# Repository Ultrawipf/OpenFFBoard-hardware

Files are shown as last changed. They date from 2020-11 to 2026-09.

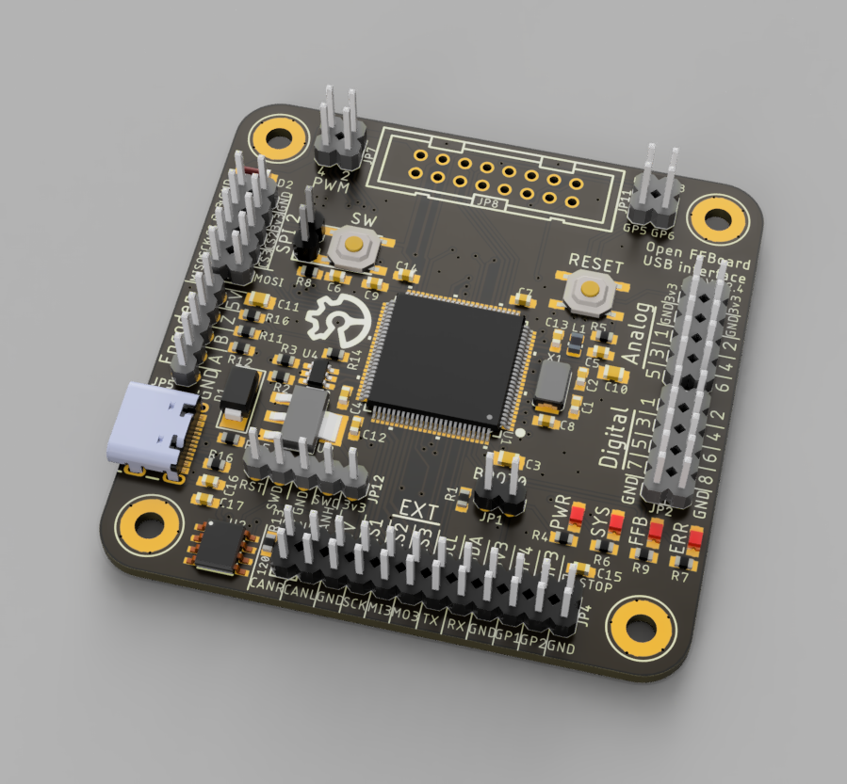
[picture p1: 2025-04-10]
OpenFFBoard-main/V1.2.4 F407/3D/OpenFFBoard_F407_1.2.4_render1.PNG

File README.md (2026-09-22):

# OpenFFBoard-hardware
This contains the hardware designs of the OpenFFBoard

These are work in progress.
No guarantee for functionality or safety! The designs are experimental and may change at any time.
The firmware is available in the main [OpenFFBoard](https://github.com/Ultrawipf/OpenFFBoard) git.

This project requires soldering of many fine pitched parts including QFN. Availability of components may change over time so check for alternatives if something is not available.
The motor driver should be made with 2oz copper layers for best thermal performance!

The firmware may run on some third party development kits but as they have different pinouts and missing peripherals this is not recommended.

## Buy official kits
* [Elecrow](https://www.elecrow.com/open-ffboard-stm32f407-usb-interface-only.html)
* [Lectronz](https://www.lectronz.com/stores/gigawipf)
* [Tindie](https://www.tindie.com/stores/gigawipf/) or Discord.

Check the [Discord](https://discord.com/invite/gHtnEcP) and [project page](https://hackaday.io/project/163904-open-ffboard) for updates.

---

### LICENSE NOTE: The root license applies to all subfolders NOT containing their own LICENSE file. If a subfolder contains a different LICENSE file this different license applies to all subfolders below this LICENSE file.

**If you want to sell any hardware of this project yourself i would kindly ask you to get in contact with me ([mail](mailto:ffboard@y-richter.de) or Discord)**

## Changelog
### TMC Driver:

#### 1.1: (Prerelease prototype)
- Added filtering for Hall and Encoder inputs.
- Separated TMC and STM VM sense dividers

#### 1.2: (Major redesign)
- Using TMC4671-LA production version
- Added 5V buck converter
- Added emergency shutdown method by pulling enable low
- Rotated power stage. Moved all motor connectors to one side
- Moved analog encoder pins and routed differential inputs out
- Improved vcore impedance
- Increased encoder filter frequencies
- Reduced resistance of sense dividers
- Switched LM5050 to LM74700
- Space for 2 VM capacitors
- Improved mosfet protection
- Added temperature sensor pads on AGPI-B
- 50x50+100mm screw holes

#### 1.2 fix:
- Fixed silkscreen (R18 and R19 swapped)
- Modified some labels
- Added 33k gate pulldown for brake resistor
- Moved and resized vias in motor driver part (Manufacturing reliability)
- Tented vias

#### 1.2.2 (HALL):
- Redesigned power stage to use hall sensors (LEM GO SME and TMCS1100)
- Changed buffers to 74LV17APWJ
- Added opamp for TMC inputs (temperature and voltage sensing)
- Used opamp as comparator for hardware brake resistor activation point (~65V)
  
### 1.3.3:
- Analog section with separate LDO
- Support for more current sensors (ACS724)
- Optimized gate driver circuit w. resistors and diodes
- More separation between analog and power sections

### STM USB Interface:
#### 1.1:
- Initial prototype
- STM32F411RE based
- Only supports TMC4671 driver
- Only one SPI2 CS

#### 1.2:
- STM32F407VG
- Reserved PWM pins
- 3 CS pins per SPI
- CAN bus
- Reserved E-Stop
- USB Vbus sense
- separated ADCs for vsense and analog in
- LEDs moved
- Added FFBoard logo
- Changed USB diode to SMC
- Added zener pad on 5V
- Removed encoder buffer
- Higher value pwr led resistor

#### 1.2.1:
- Fixed some labels
- Moved USB socket and terminals slightly to the corners (Big usb plugs might interfere with the pins)
- Changed crystal load capacitors to lower values. (F407 DFU is very sensitive and does not work reliably with too high value caps)
- Added E-Stop capacitor against noise triggering it
- Tented vias

#### 1.2.2
- Swapped (Previously unused) Encoder Z pin from pin 65 to pin 62 because of interrupt conflicts with the DRV flag pin

#### 1.2.3
- USB-C instead of micro USB
- SPI1 uses a 2 row header
- Additional USB protections

#### 1.2.4
- Moved EXT header slightly
- Used 2 extra jumper pins for CAN termination instead of solderjumper

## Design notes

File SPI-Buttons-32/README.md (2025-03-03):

# Shift register button module

This module allows the connection of up to 32 (or more if chained) buttons to any spi capable microcontroller or as a button source in the OpenFFBoard firmware.

### Connections
* V+ - 3,3V (or 5V)
* OUT - MISO of controller
* CS (Latch) - CS pin of controller
* CLK - SCK
* GND - GND

* IN - OUT of previous module
* Buttons between GND and any input pin

### Configuration in OpenFFBoard

Select SPI button source, select 74HC165 mode and invert buttons and the amount of used buttons (up to 32 for 1, up to 64 for 2 modules)

### CS options

In the default configuration MISO is active with CS HIGH (Bare 74HC165 compatible mode).
Connecting R34 instead of R33 changes this to CS LOW active (SPI compatible mode).
The tristate output mode can be disabled by removing R35.

Mode | R33 | R34 | R35
-|-|-|-
CS HIGH w. tristate | ✅ | ❌ | ✅
CS LOW w. tristate | ❌ | ✅ | ✅
CS HIGH wo. tristate | ✅ | ❌ | ❌
CS HIGH wo. tristate | ❌ | ✅ | ❌

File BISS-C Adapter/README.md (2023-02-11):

## BISS-C module

This module allows the OpenFFBoard to use its SPI3 (EXT) header to communicate with common BISS-C encoders like the JKD-4-22PF-G05BL (used on Mige motors).

The SUB-D 15 female connector matches the pinout of Mige motors and some others directly.

The CS pin connection is optional. When left disconnected or low the transceivers are active, when high the transceivers are off.

The BISS-C encoder module can only be used with certain motor driver modes:

-   TMC via forwarding

-   VESC as secondary encoder

-   PWM

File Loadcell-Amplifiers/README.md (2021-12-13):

## INA333 3-wire Loadcell amplifier

Connections:
###
- Vin   :   3.3V/5V supply and load cell positive
- GND   :   GND and load cell negative
- IN    :   Load cell center/signal
- OUT   :   Amplified signal. Connect to ADC input

Gain setting: 10-1000, Clockwise rotation to increase
Offset: Clockwise to move the output up, ccw to move the output down to GND

Retune the offset when changing the gain and carefully check the output voltage to get the offset perfect.

The CPL and BOM files contain LCSC part numbers and be used on [JLCPCB](jlcpcb.com/).

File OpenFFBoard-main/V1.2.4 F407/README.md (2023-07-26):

### FFBoard main USB interface F407VG
This is the heart of the Open FFBoard.
It runs the FFBoard firmware and interfaces with all your peripherals and motor drivers.

V1.2.3 and 1.2.4 is a USB-C version and adds additional USB protections.
The SPI1 port layout had to change to 2 rows instead of 1.

#### How to order yourself
You can order this board directly via [jlcpcb.com](https://jlcpcb.com/?from=Gigawipf).

The BOM and component placement files are available in the JLC assembly folder and already formatted with matching LCSC part numbers.

Everything apart from the headers can be directly assembled by JLC including the USB socket.

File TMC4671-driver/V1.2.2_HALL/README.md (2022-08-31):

# OpenFFBoard TMC4671 driver 1.2.2

Note: this is an experimental version for testing hall sensors. The 1.2 is shunt based.

Some parts may be difficult to source. The manufacturing files were made during a time where alternatives had to be found for some parts.

For the TMC1100 the SJ1 and SJ2 2.5V ref jumpers must be shorted. The LEM GO provides its own reference and the SJ1 and SJ2 must be left disconnected for best noise performance and C27 and C28 MUST be left blank!

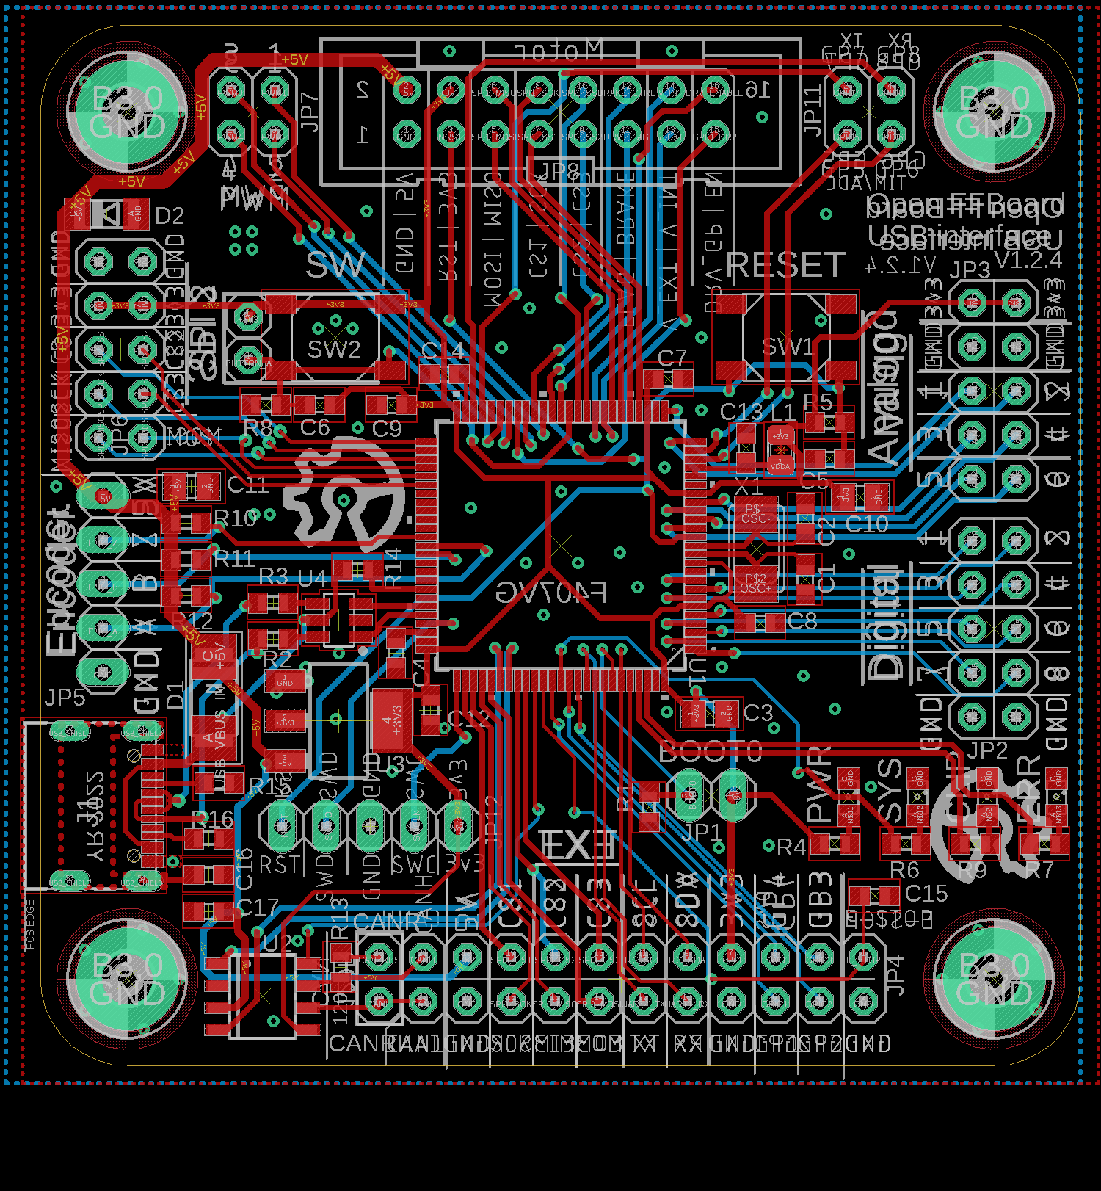
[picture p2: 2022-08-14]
OpenFFBoard-main/V1.2.4 F407/board.png

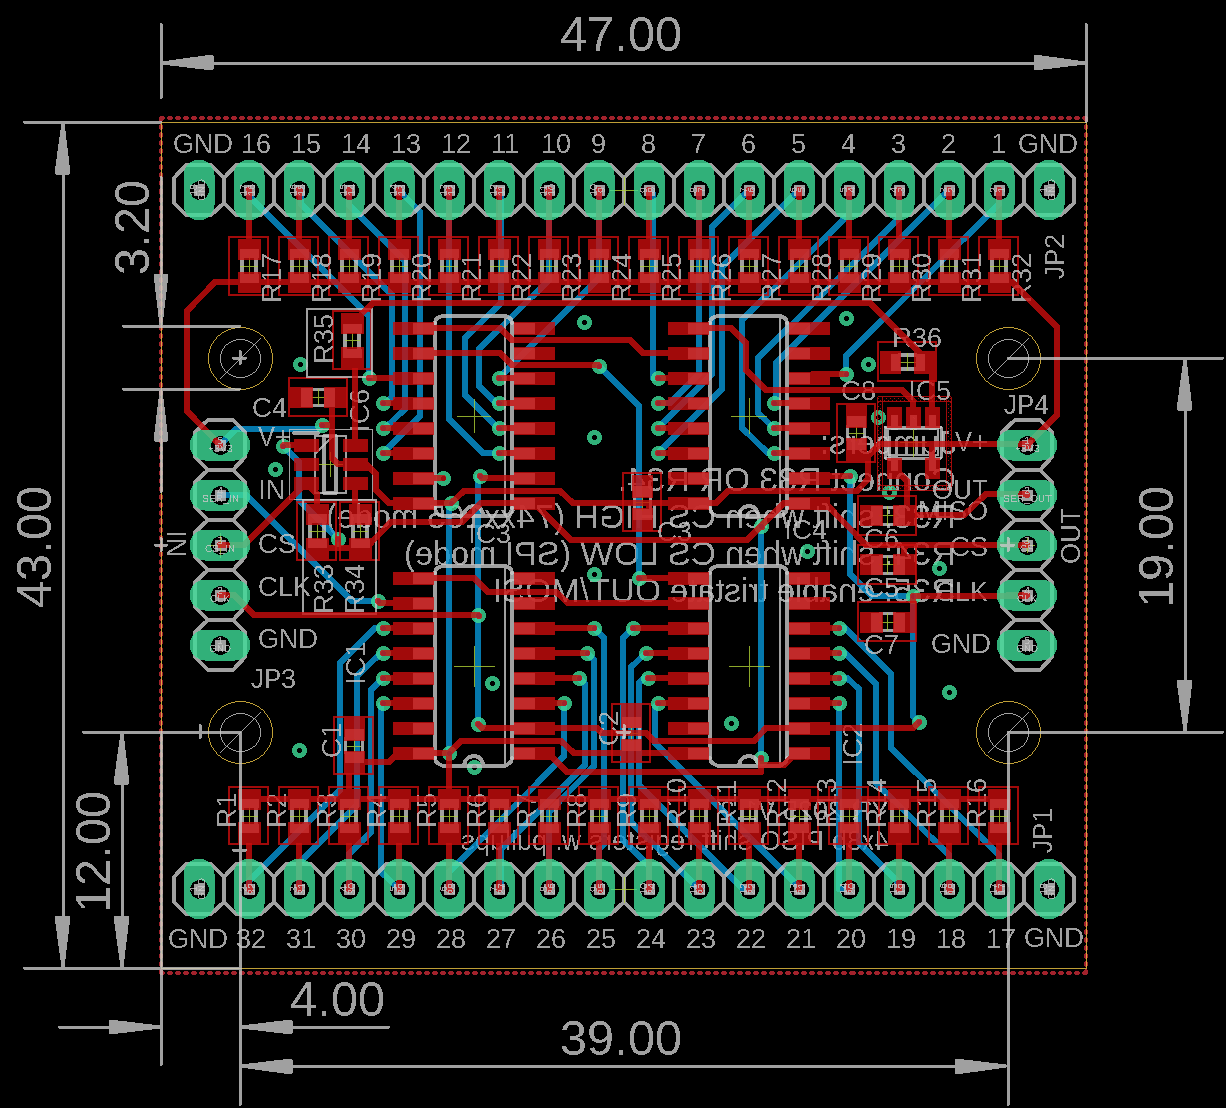
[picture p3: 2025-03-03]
SPI-Buttons-32/pcb.png

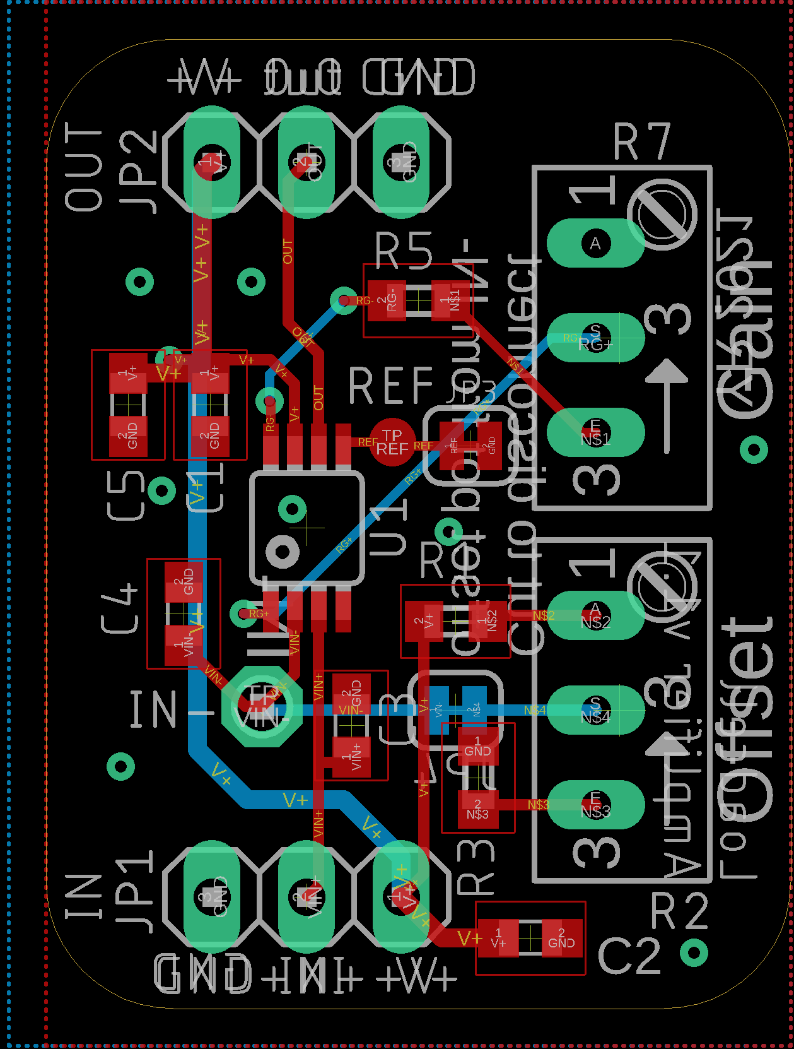
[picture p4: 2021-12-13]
Loadcell-Amplifiers/boardview.png

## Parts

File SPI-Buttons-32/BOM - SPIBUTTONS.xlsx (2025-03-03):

Comment | Designator | Footprint | LCSC Part #
1x18 pinheader | JP1, JP2 | 1X18
1x5 pinheader | JP3, JP4 | 1X05
10k resistor | R1, R2, R3, R4, R5, R6, R7, R8, R9, R10, R11, R12, R13, R14, R15, R16, R17, R18, R19, R20, R21, R22, R23, R24, R25, R26, R27, R28, R29, R30, R31, R32,R36 | R0603 | C25804
1µF capacitor | C1, C2, C3, C4,C8 | C0603 | C15849
74HC165D | IC1, IC2, IC3, IC4 | SO16 | C5613
0R | R35,R33 | R0603 | C21189
SN74LVC2G14DBV | IC6 | SOT23-6 | C12401
74LVC1G125DBV | IC5 | SOT23-5 | C23654

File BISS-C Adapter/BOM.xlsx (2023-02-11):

Comment | Designator | Footprint
SUB-D | X1
5p header 90° | JP1
100nF | C1, C2 | C0603
4.7uF | C3 | C0603
RS485 transceiver | IC1, IC2 | SOIC-8
10k | R1,R2 | R0603
Nmos | Q1 | SOT-23

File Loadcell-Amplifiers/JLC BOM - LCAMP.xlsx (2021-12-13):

Comment | Designator | Footprint | LCSC Part #
INA333 | U1 | MSOP-8 | C19450
10k pot | R2,R7 | THT | C118954
1µ Capacitor | C2,C3,C5 | C0603 | C15849
4.7k Resistor | R1, R3 | R0603 | C23162
47 Ohm Resistor | R5 | R0603 | C23182
100n Capacitor | C4, C1 | C0603 | C14663

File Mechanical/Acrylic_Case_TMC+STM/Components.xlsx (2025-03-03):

Amount | Type | File/Link
1 | Bottom cover 3mm clear acrylic | Bottom_nosides.dxf
1 | Top cover 3mm clear acrylic | Top_nosides.dxf
6 | Nylon M3x6 screw
6 | Nylon M3 nut
10 | Nylon M3x6+6 Standoff
2 | Nylon M3x18+6 Standoff
2 | 0.5mm or 0.6mm M3 washer

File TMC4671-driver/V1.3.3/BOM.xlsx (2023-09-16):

Comment | Designator | Footprint | Notes
3.3V Ldo 1117 | U21 | SOT223
1.5k | R16, R22, R24, R29, R31, R40, R41, R42 | R0603
100nF | C1, C3, C4, C5, C6, C7, C8, C15, C16, C17, C19, C20, C21, C22, C23, C24, C26, C33, C35, C36 | C0603
10k | R2, R3, R15, R17, R18, R26, R28, R46 | R0603
ERTJ1VR103J | R30 | R0603 | digikey https://www.digikey.de/en/products/detail/panasonic-electronic-components/ERT-J1VR103J/269353 lcsc C525381
10µH LQH43PN100M26L | L2 | L4532P | digikey
4.7nF | C42, C43,C29, C30, C31 | C0603 |  | Depends on sensor variant
1µF | C11, C12, C13, C14, C37 | C1206
15 | R4, R5, R6, R7, R8, R9, R10, R11 | R0603
220µH 74404084221 | L1 | 8MM INDUCTOR | digikey
25MHz | Y1 | ECS-327KE-TR
294k | R25, R27, R43 | R0805
33k | R12, R13, R14, R20, R21 | R0603
4.7k | R34, R35, R36, R37, R38, R39 | R0603
10µF | C2, C18, C25, C32, C34, C39, C41 | C0805
47k | R33 | R0603 |  | Brake resistor emergency point
593D476X0016D2TE3 | C38 | CAPPM7343X310N
680µF EEU-FS1K681B | C9, C10 | E7,5-16 | https://www.digikey.de/en/products/detail/panasonic-electronic-components/EEU-FS1K681B/9597098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 | https://www.arrow.com/en/products/eeu-fs1k681b/panasonic?q=EEU-FS1K681B
71.5k | R23, R32, R44, R45 | R0805
74LV17APWJ | U19 | TSSOP14 | digikey
AP3012KTR-G1 | U24 | SOT23-5L
NTMFSC2D9N08H | U8, U9, U10, U11, U12, U13, U15, U16, U17,U22 | POWERTFDN8 | Or FDMS86181, BSC030N08NS5 (20ohm gates minimum)
BZX384-XXX | D6, D7, D8, D11 | SOD323-R
Green | LED1 | SML0805
HV >100V | D2, D3, D4, D5, D12, D14 | SOD-123FL | Must handle 500mA+
LM5109BSD | U2, U3, U4, U5 | SDC08A
LM74700-Q1 | U20 | SOT23-6 | https://www.digikey.de/en/products/detail/texas-instruments/LM74700QDBVTQ1/9953058
LV low drop diode (<10V) | D1, D9, D10, D16 | SOD-123FL | Fast gate discharge
max5035dasa | U23 | 8-SOIC
MCP1402T-E | U14 | SOT23-5L
MCP6004 | U18 | TSSOP14
TMC4671 | U1 | QFN76_10P5X6P5
5V LDO 1117 | U25 | SOT223
STPS30120DJF-TR | (U22) | PowerFLAT-5x6 | If no LM74700 is used. Otherwise use another mosfet here
SMA HV diode | D15 | SMA Diode | For DC converter
ACS724 (https://www.lcsc.com/product-detail/Current-Sensors_Allegro-MicroSystems-LLC-ACS724LLCTR-30AB-T_C141715.html) | U6,U7
0 | R50,R51,R47, R48 | R0603 | For ACS724
0 | sj1,sj2,SJ3 | R0805 | For ACS724
47k | R1 | R0603 | 5v FB for max5035D
15k | R49 | R0603

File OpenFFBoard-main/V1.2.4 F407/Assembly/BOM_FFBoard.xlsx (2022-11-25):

Comment | Designator | Footprint | LCSC Part #（optional）
3V3 LDO xx1117 | U3 | SOT223 | C6186 (https://lcsc.com/product-detail/Low-Dropout-Regulators-LDO_AMS_AMS1117-3-3_AMS1117-3-3_C6186.html/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)
100nF | C5, C6, C7, C8, C9, C12, C13, C15, C16, C17 | C0603 | C14663 (https://lcsc.com/product-detail/Multilayer-Ceramic-Capacitors-MLCC-SMD-SMT_YAGEO-CC0603KRX7R9BB104_C14663.html)
USB-C connector | J1 | USB-C | C319148
10k | R1, R5, R8, R14 | R0603 | C25804 (https://lcsc.com/product-detail/Chip-Resistor-Surface-Mount_Uniroyal-Elec-0603WAF1002T5E_C25804.html/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)
120 | R13 | R0603 | C22787 (https://lcsc.com/product-detail/Chip-Resistor-Surface-Mount_Uniroyal-Elec-0603WAF1200T5E_C22787.html/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)
1k | R4 | R0603 | C21190 (https://lcsc.com/product-detail/Chip-Resistor-Surface-Mount_Uniroyal-Elec-0603WAF1001T5E_C21190.html/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)
2.2µF | C4, C14 | C0603 | C23630 (https://lcsc.com/product-detail/Multilayer-Ceramic-Capacitors-MLCC-SMD-SMT_SAMSUNG_CL10A225KO8NNNC_2-2uF-225-10-16V_C23630.html/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)
22 | R2, R3 | R0603 | C23345 (https://lcsc.com/product-detail/Chip-Resistor-Surface-Mount_Uniroyal-Elec-0603WAF220JT5E_C23345.html/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)
15pF | C1, C2 | C0603 | C1644 (https://lcsc.com/product-detail/Multilayer-Ceramic-Capacitors-MLCC-SMD-SMT_Samsung-Electro-Mechanics-CL10C150JB8NNNC_C1644.html)
330 | R6, R7, R9 | R0603 | C23138 (https://lcsc.com/product-detail/Chip-Resistor-Surface-Mount_Uniroyal-Elec-0603WAF3300T5E_C23138.html/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)
5.1k | R10, R11, R12, R15, R16 | R0603 | C23186
4.7uF | C3, C10, C11 | C0805 | C1779 (https://lcsc.com/product-detail/Multilayer-Ceramic-Capacitors-MLCC-SMD-SMT_SAMSUNG_CL21A475KAQNNNE_4-7uF-475-10-25V_C1779.html/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)
8MHz Crystal | X1 | NX5032 | C115962 (https://lcsc.com/product-detail/SMD-Crystal-Resonators_Yangxing-Tech-X50328MSB2GI_C115962.html/?href=jlc-SMT)
Ferrite | L1 | BLM21PG331SN1D | C1017 (https://lcsc.com/product-detail/Beads_Sunlord-GZ2012D601TF_C1017.html/?href=jlc-SMT)
LV Diode | D1 | SMADIODE | C2480 (https://lcsc.com/product-detail/Schottky-Barrier-Diodes-SBD_MDD-Microdiode-Electronics-SS14_C2480.html/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)
STM32F407VGT6 | U1 | LQFP100-14X14MM | C12345 (https://lcsc.com/product-detail/ST-Microelectronics_STMicroelectronics-STM32F407VGT6_C12345.html)
TJA1051T/3 | U2 | SOT96-1 | C38695 (https://lcsc.com/product-detail/CAN_NXP_TJA1051T-3-1J_TJA1051T-3-1J_C38695.html/?href=jlc-SMT)
Pushbutton | SW1, SW2 | 5.1mm | C318884 (https://lcsc.com/product-detail/Tactile-Switches_XKB-Connectivity-TS-1187A-B-A-B_C318884.html)
ZMM5V6 | D2 | MINIMELF | C8062 (https://lcsc.com/product-detail/Zener-Diodes_ST-Semtech-ZMM5V6_C8062.html)
blue | LED2 | CHIPLED_0805 | C189307
green | LED1 | CHIPLED_0805 | C2297 (https://lcsc.com/product-detail/Light-Emitting-Diodes-LED_Hubei-KENTO-Elec-C2297_C2297.html)
red | LED3 | CHIPLED_0805 | C84256 (https://lcsc.com/product-detail/Light-Emitting-Diodes-LED_Red-LED-SMDLED-80-180mcd_C84256.html/?href=jlc-SMT)
yellow | LED4 | CHIPLED_0805 | C2296 (https://lcsc.com/product-detail/Light-Emitting-Diodes-LED_Yellow-light-0805-Highlighted_C2296.html/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)
USB ESD protection | U4 | SOT-23-6 | C2827654

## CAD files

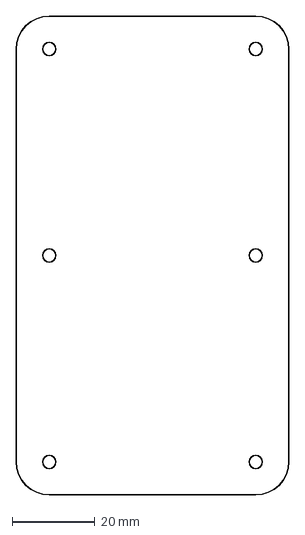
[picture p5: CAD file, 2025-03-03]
Mechanical/Acrylic_Case_TMC+STM/Bottom_nosides.dxf
66.0 x 116.0 mm

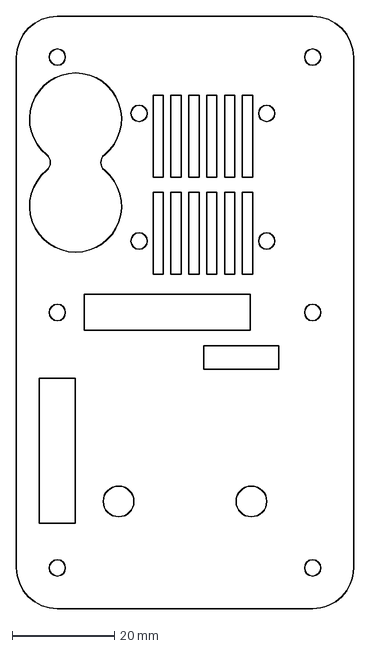
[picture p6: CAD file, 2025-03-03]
Mechanical/Acrylic_Case_TMC+STM/Top_nosides.dxf
66.0 x 116.0 mm

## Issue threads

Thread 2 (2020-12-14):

TMC4671 Driver Obsolete Parts

willson556, 2020-12-14:
Hi,

I started trying to put together an order on Digikey based on the [BOM](https://github.com/Ultrawipf/OpenFFBoard-hardware/blob/1a2b9acf6f00e4338b6bcb587ea3f9aa6fa2637c/TMC4671-driver/BOM.ods) and it looks like a couple of the parts are obsolete:

- `LM5109BSD` replaced by `LM5109BSD/NOPB`
- `MAX5033BASA` replaced by `MAX5033BASA+`

I've uploaded the Digikey BOM I ended up using in case it's helpful to anyone else -- it should be possible to directly import [Bom_8468218.xlsx](https://github.com/Ultrawipf/OpenFFBoard-hardware/files/5687039/Bom_8468218.xlsx) into Digkey's BOM Manager.

choikiyeon, 2021-03-04:
CPL file plz

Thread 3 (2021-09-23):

Swapped encoder Z pin on F407 board not updated in schematic

bjanders, 2021-09-23:
In commit 31e6b57c136df8f5c7ae9fc0cd2735a78ad29ff5 the encoder Z pin was updated on the board, but not in the schematic, and now the board and schematic are out of sync in the git repository. I verified that the board and schematic were in sync before this commit.

Ultrawipf, 2021-09-26:
You are right. Updated the schematic and pdf to reflect the changes. According to eagle its back in sync for me.

Closed 2021-09-26.

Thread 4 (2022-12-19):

Use board STM32F407VET6

active-game, 2022-12-19:
Is it possible to use Stm32f407vet6 modul without your board?  if so, which pins to connect to?

blackneutron, 2023-10-29:
Did you get any answers?

Ultrawipf, 2023-10-30:
Yes you can as long as your firmware build is smaller than 512k flash. Its otherwise identical to the F407VGT6.
This is currently the case but may not be in the future. Disabling features can decrease the size as well.

Closed 2023-10-30.

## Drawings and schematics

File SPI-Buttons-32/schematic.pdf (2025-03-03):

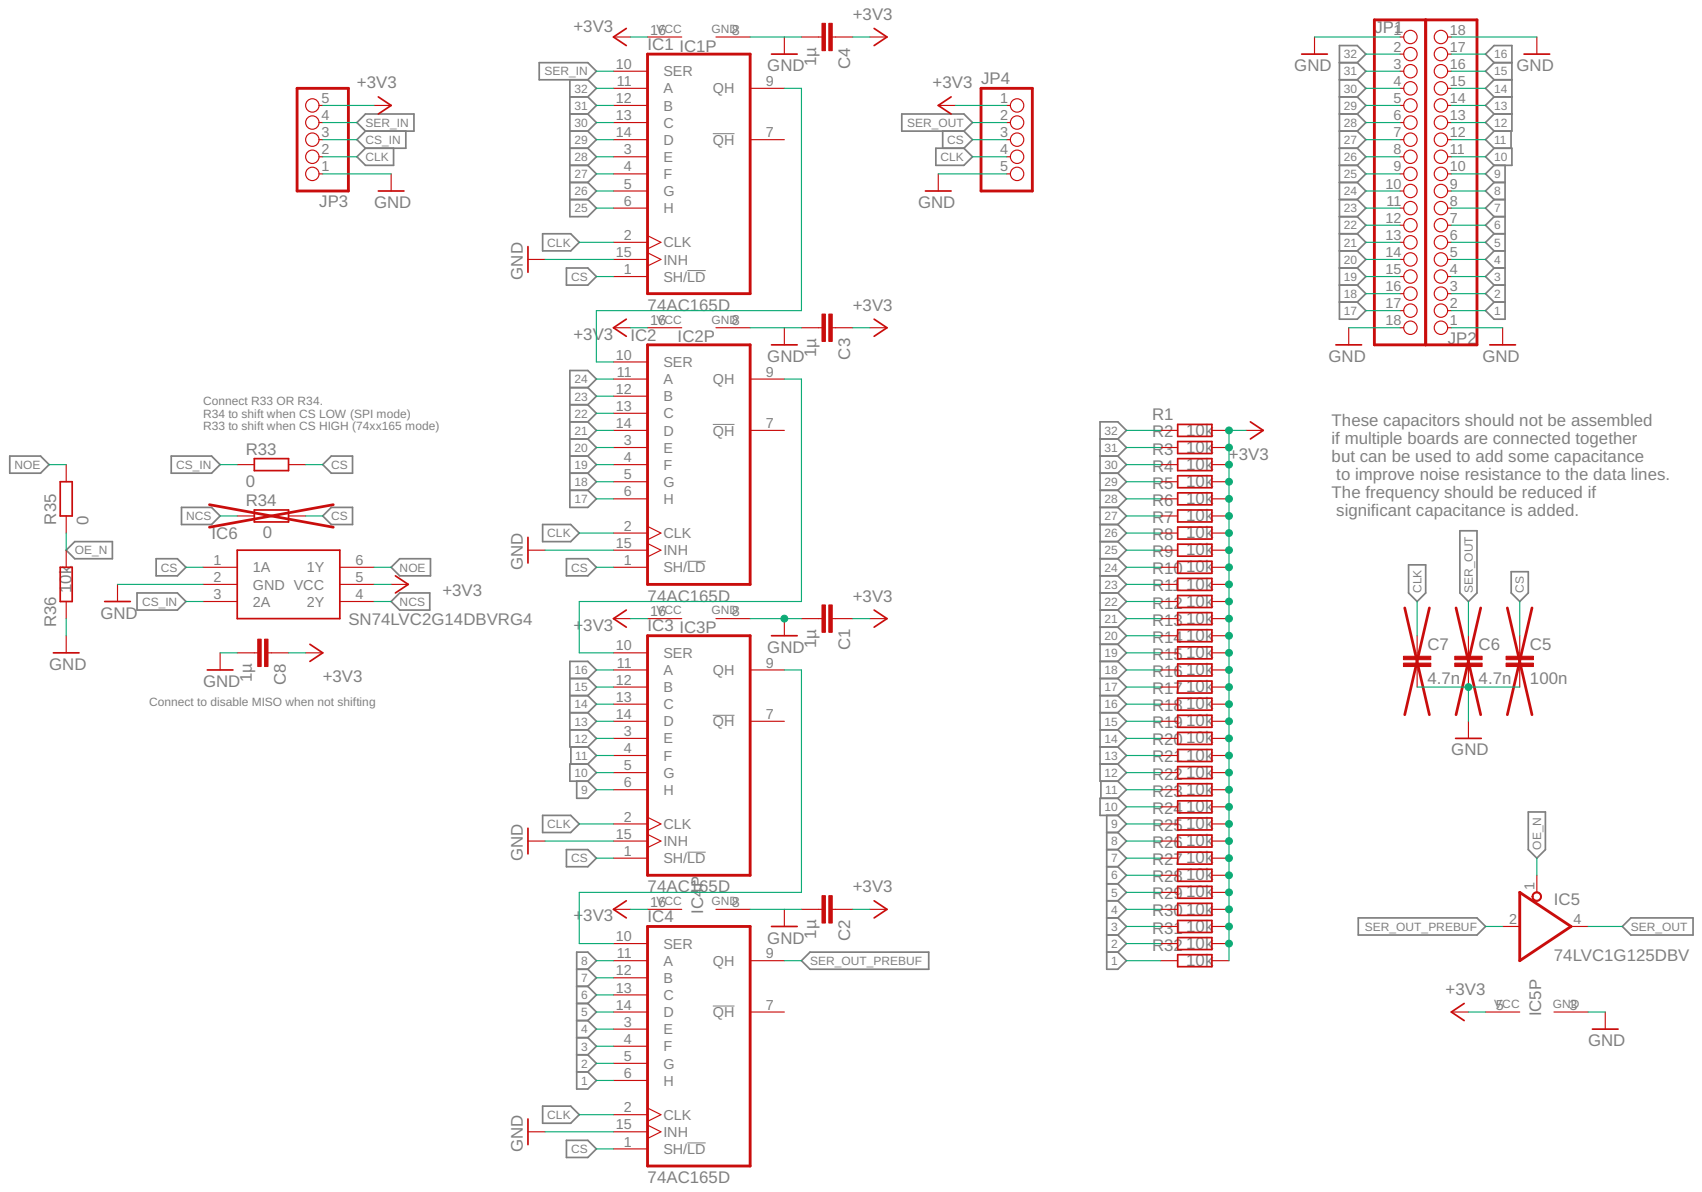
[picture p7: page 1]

GND GND

Connect R33 OR R34. R34 to shift when CS LOW (SPI mode) R33 to shift when CS HIGH (74xx165 mode)

These capacitors should not be assembled
if multiple boards are connected together but can be used to add some capacitance

to improve noise resistance to the data lines. The frequency should be reduced if significant capacitance is added.

Connect to disable MISO when not shifting

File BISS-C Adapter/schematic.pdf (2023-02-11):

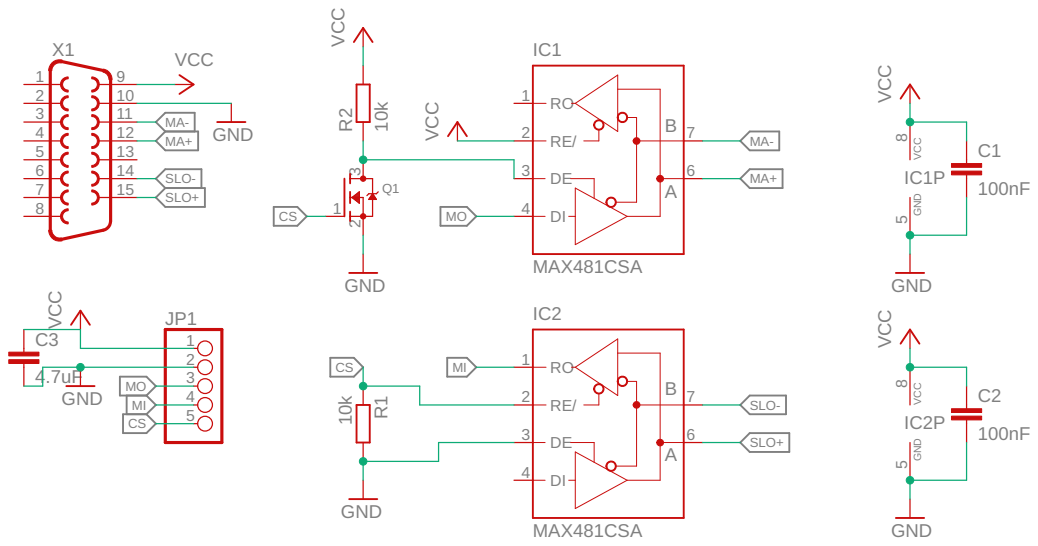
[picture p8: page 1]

VCC VCC 100nF 100nF GND GND MAX481CSA MAX481CSA VCC GND VCCGND 4.7uF 10k GND VCC 10k GND VCC 12345678 9101112131415 X1 12345 JP1 C1 C2 AB RO 1 RE/ 2 DE 3 DI 4 67 IC1 AB RO 1 RE/ 2 DE 3 DI 4 67 IC2 GND VC 8C 5 IC1PGND VC 8C 5 IC2P C3 1 2 3 Q1 R2 R1 MI MI MO MO MA- MA- MA+ MA+ SLO- SLO- SLO+ SLO+ CS CS CS

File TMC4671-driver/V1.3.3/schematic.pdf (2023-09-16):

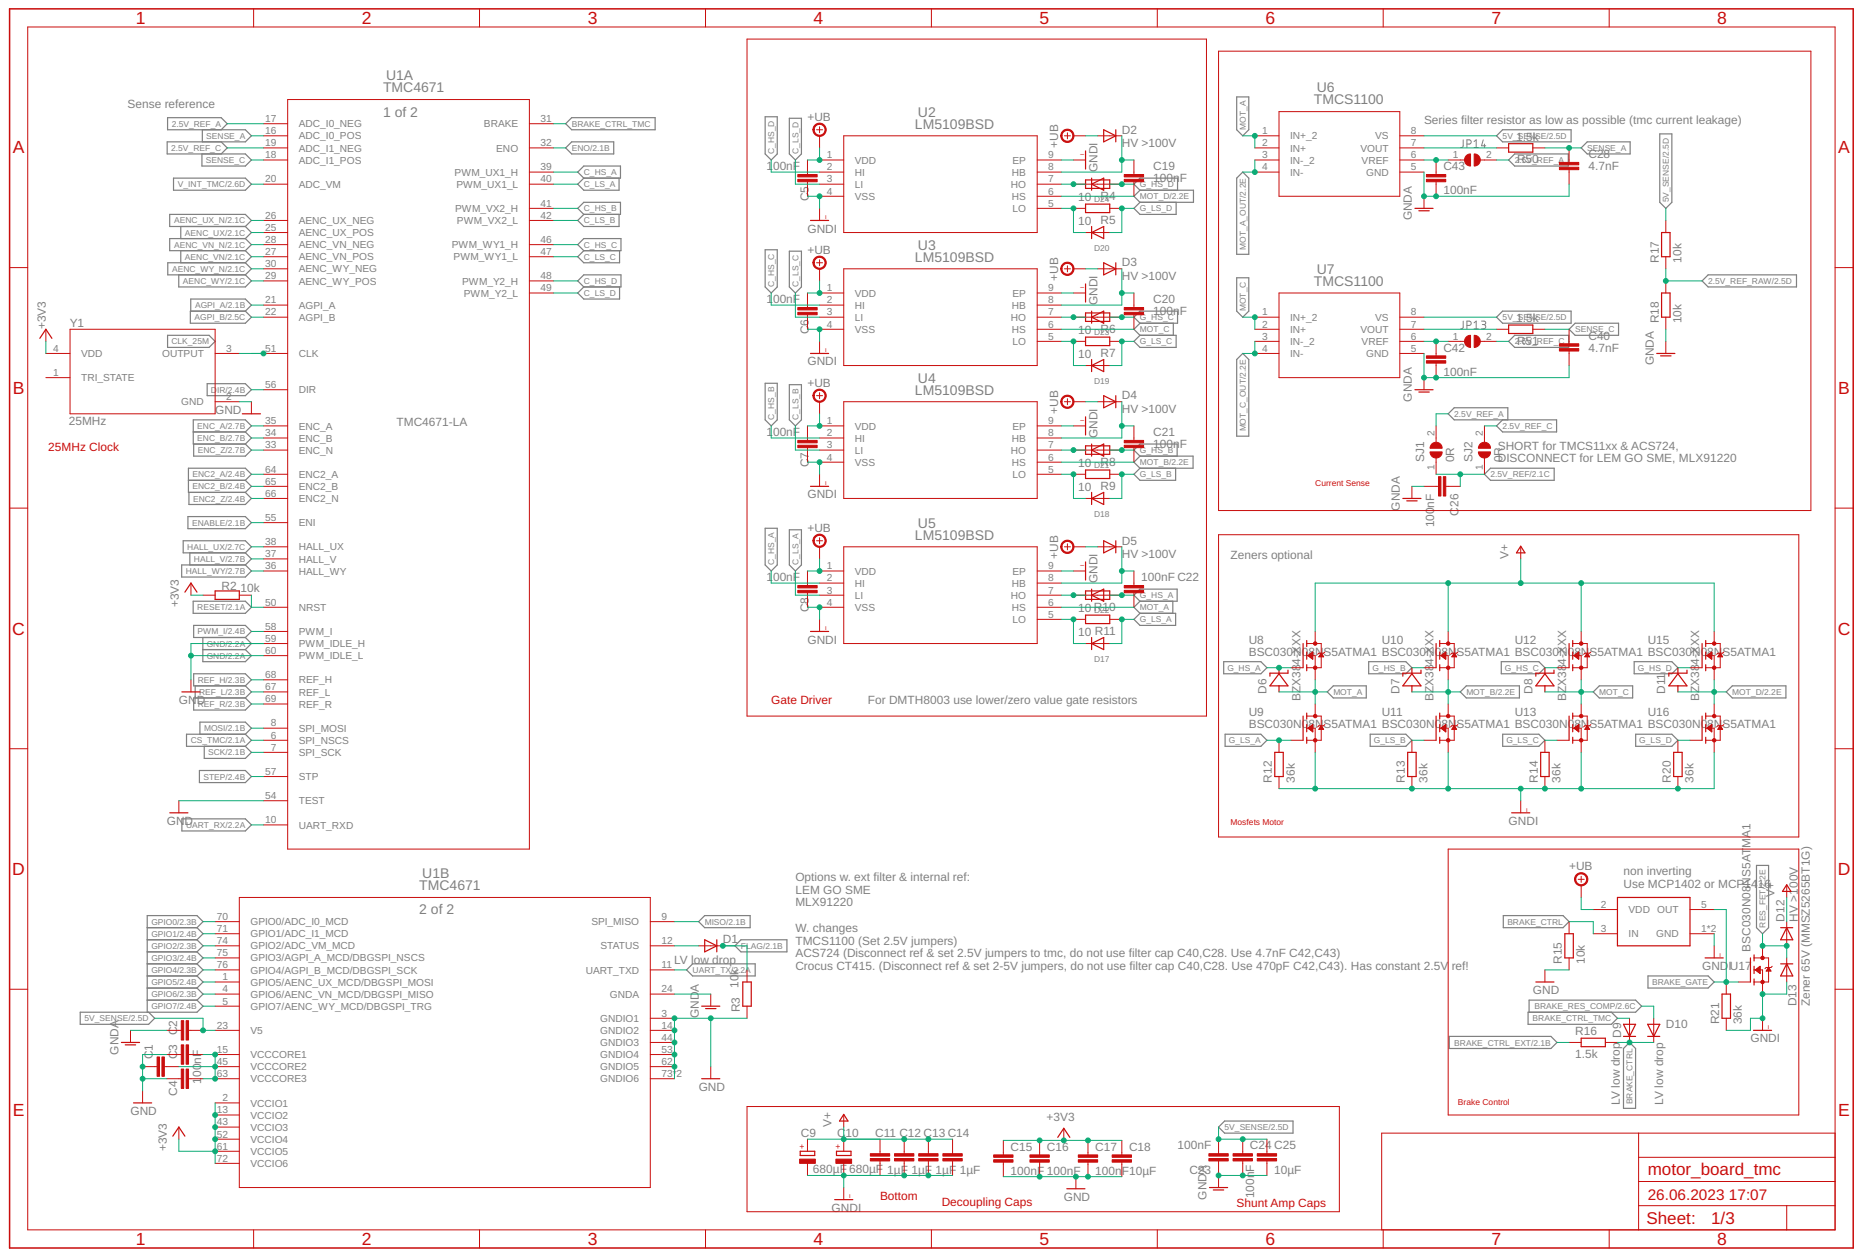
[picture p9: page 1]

Series filter resistor as low as possible (tmc current leakage)

GNDI GNDI

2.5V_REF_C
SHORT for TMCS11xx & ACS724, DISCONNECT for LEM GO SME, MLX91220

For DMTH8003 use lower/zero value gate resistors

Options w. ext filter & internal ref: LEM GO SME

ACS724 (Disconnect ref & set 2.5V jumpers to tmc, do not use filter cap C40,C28. Use 4.7nF C42,C43)

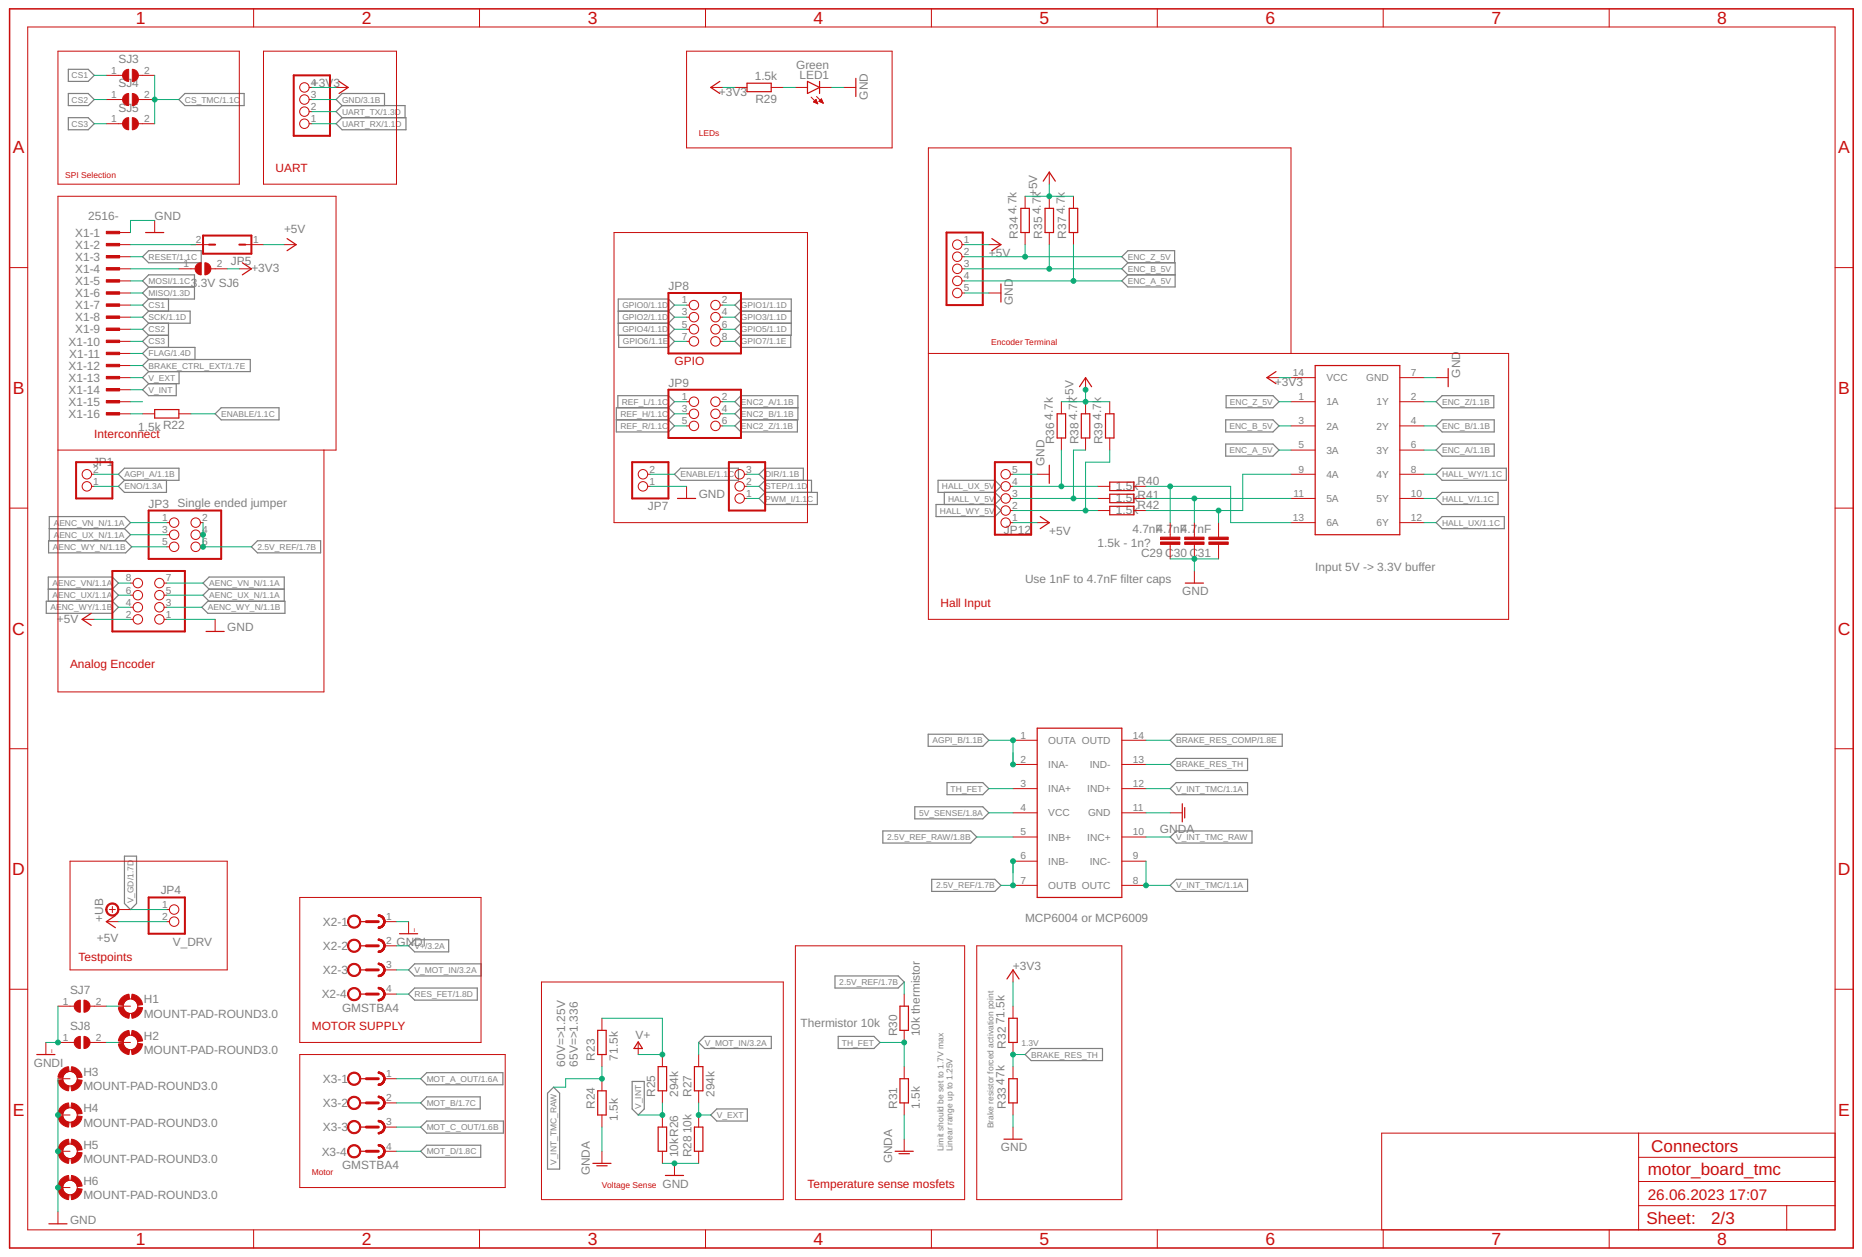
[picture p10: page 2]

AENC_VN/1.1A
AENC_UX/1.1A
AENC_WY/1.1B | AENC_WY_N/1.1B

Use 1nF to 4.7nF filter caps

Brake resistor forced activation point

Limit should be set to 1.7V max Linear range up to 1.25V

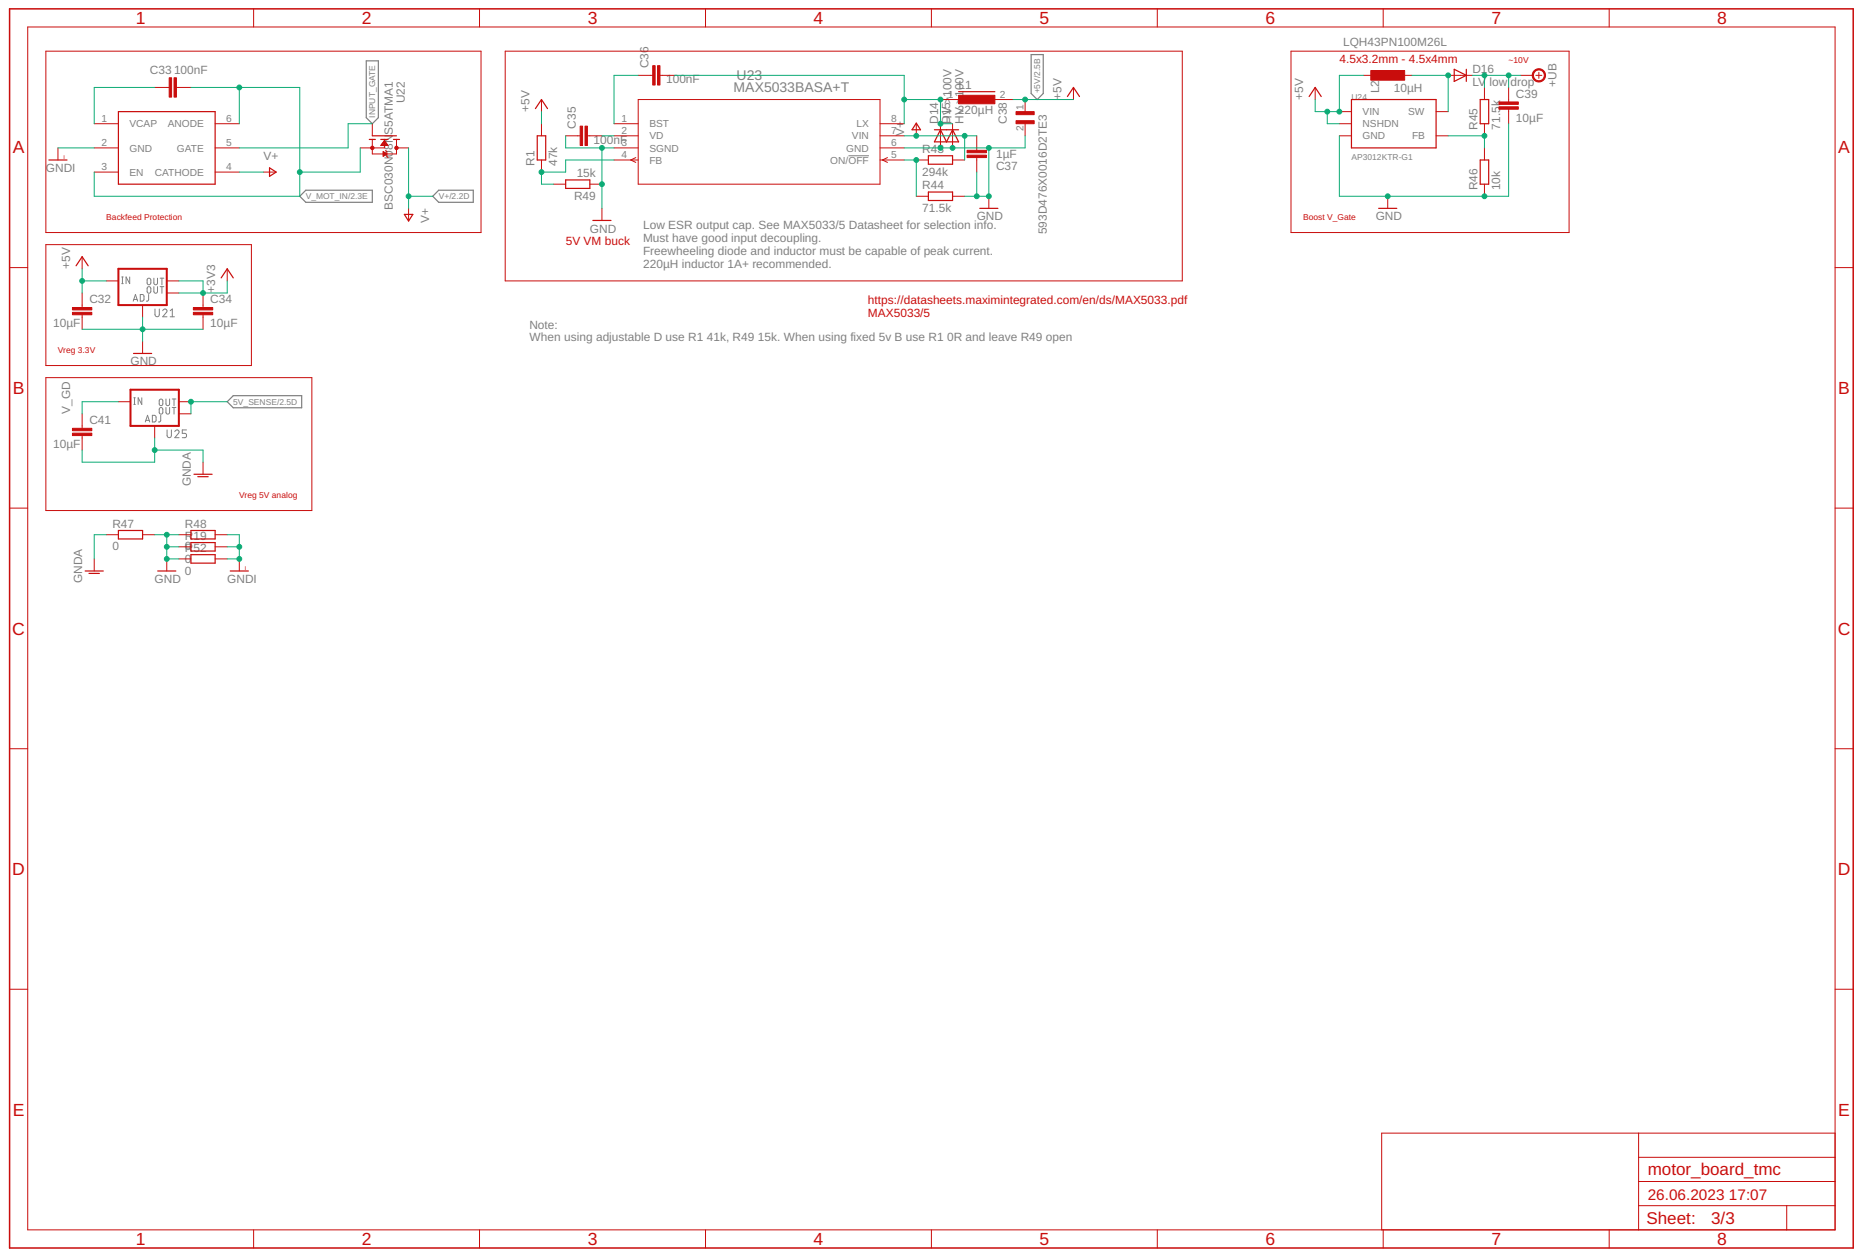
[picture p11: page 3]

Low ESR output cap. See MAX5033/5 Datasheet for selection info. Must have good input decoupling. Freewheeling diode and inductor must be capable of peak current. 220µH inductor 1A+ recommended. Note: When using adjustable D use R1 41k, R49 15k. When using fixed 5v B use R1 0R and leave R49 open

https://datasheets.maximintegrated.com/en/ds/MAX5033.pdf
MAX5033/5

Vreg 5V analog

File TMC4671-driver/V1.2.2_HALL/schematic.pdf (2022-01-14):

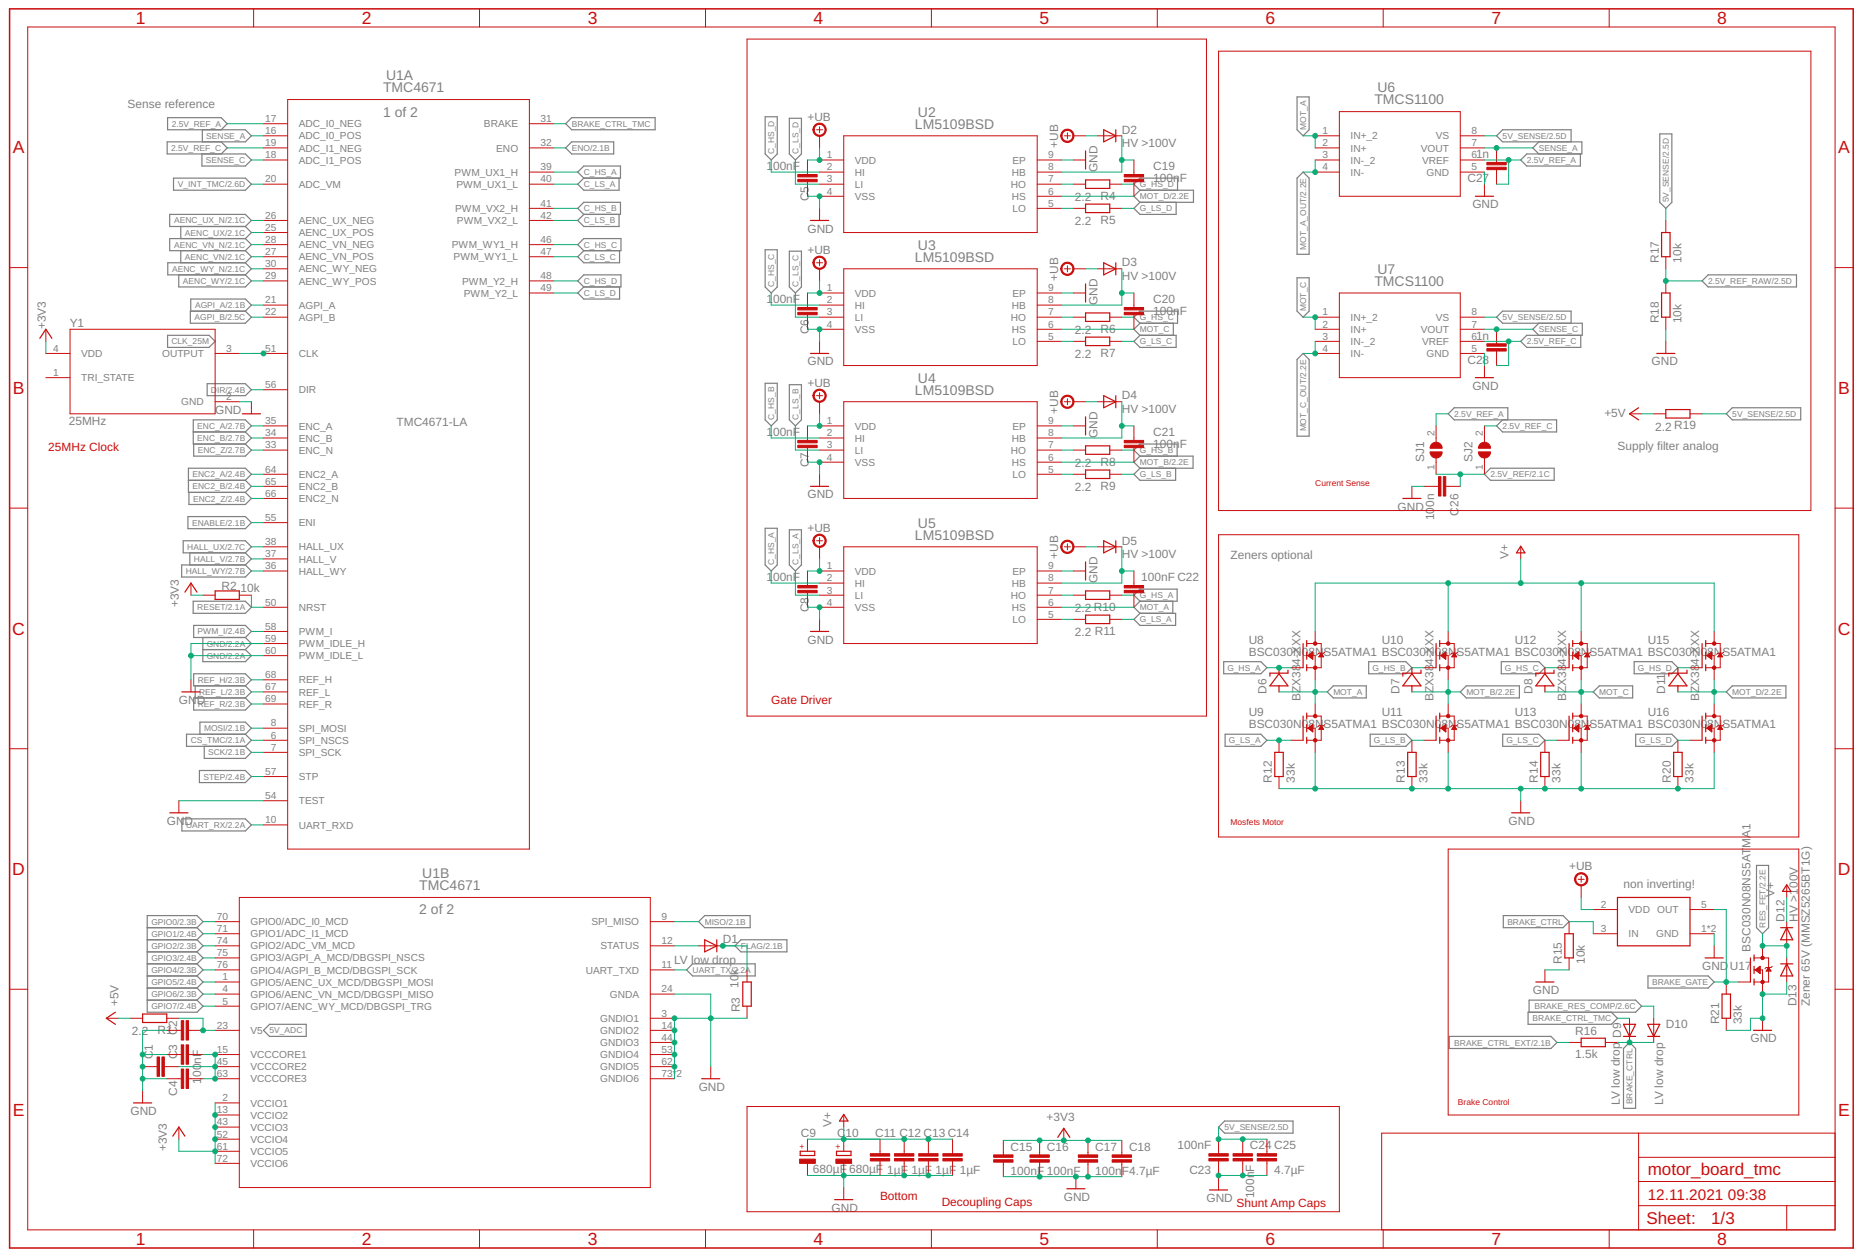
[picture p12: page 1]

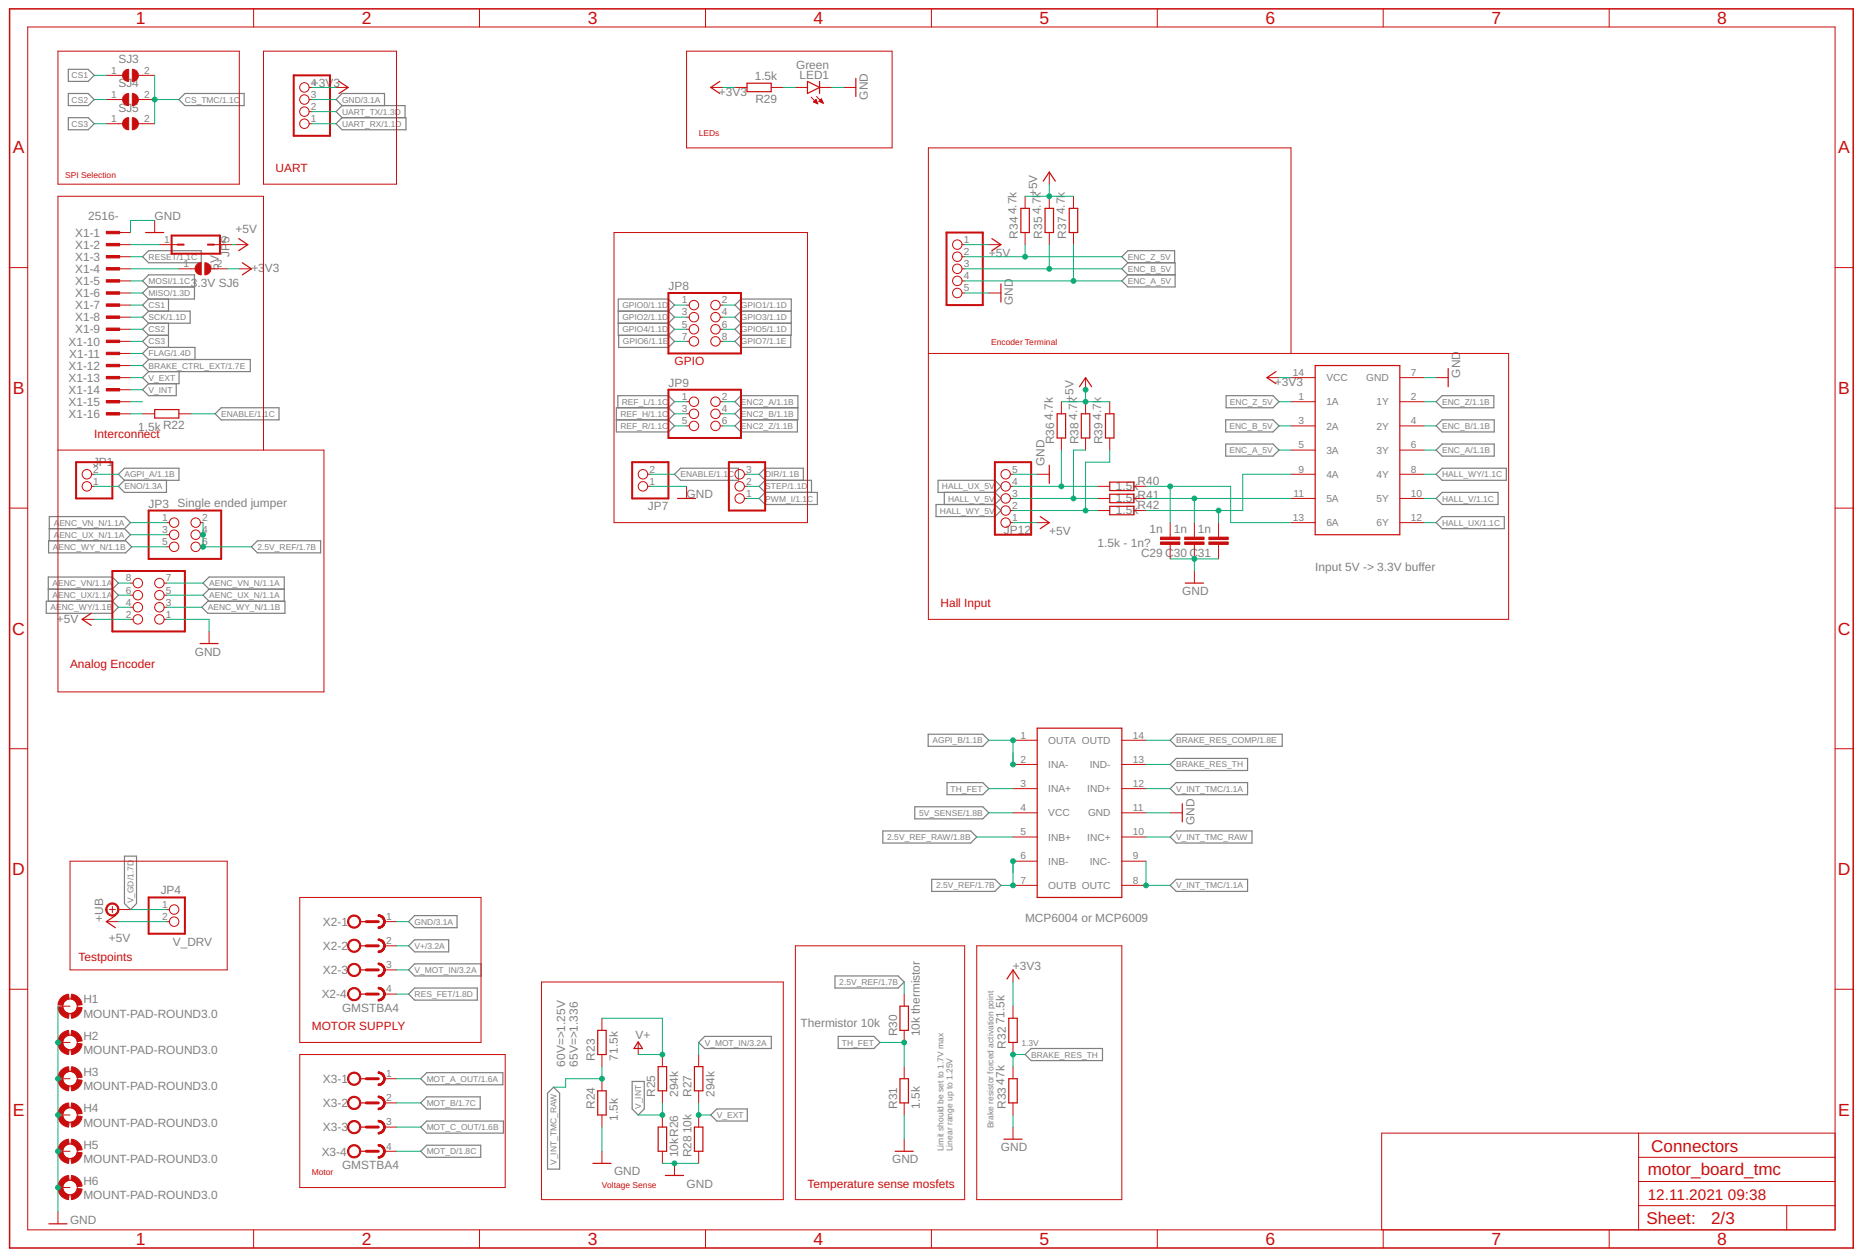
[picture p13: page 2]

AENC_VN/1.1A | AENC_VN_N/1.1A
AENC_UX/1.1A | AENC_UX_N/1.1A
AENC_WY/1.1B | AENC_WY_N/1.1B

Brake resistor forced activation point

Limit should be set to 1.7V max Linear range up to 1.25V

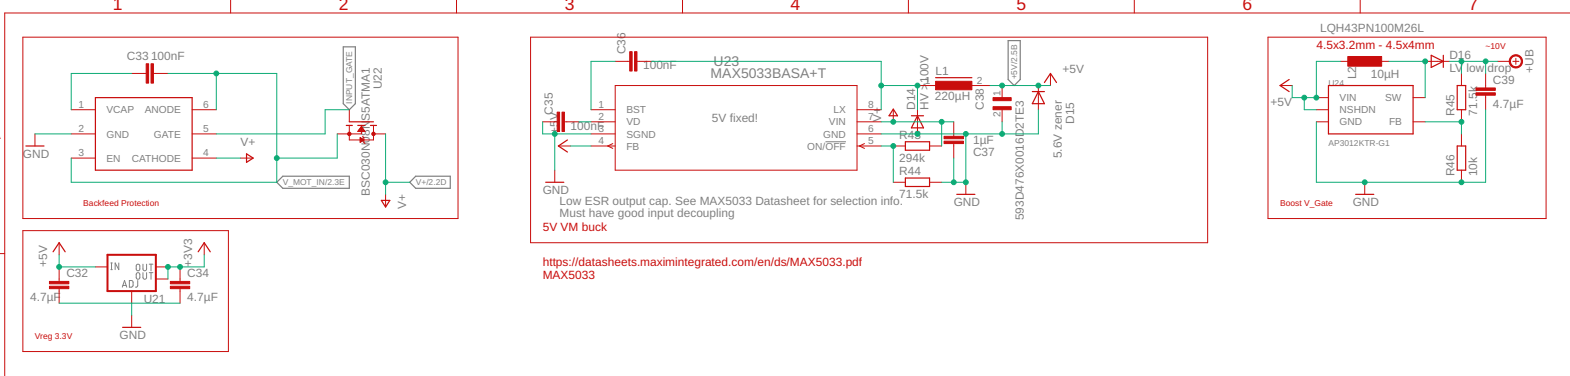
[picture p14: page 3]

Low ESR output cap. See MAX5033 Datasheet for selection info. Must have good input decoupling BSC030N08NS5ATM

https://datasheets.maximintegrated.com/en/ds/MAX5033.pdf
MAX5033

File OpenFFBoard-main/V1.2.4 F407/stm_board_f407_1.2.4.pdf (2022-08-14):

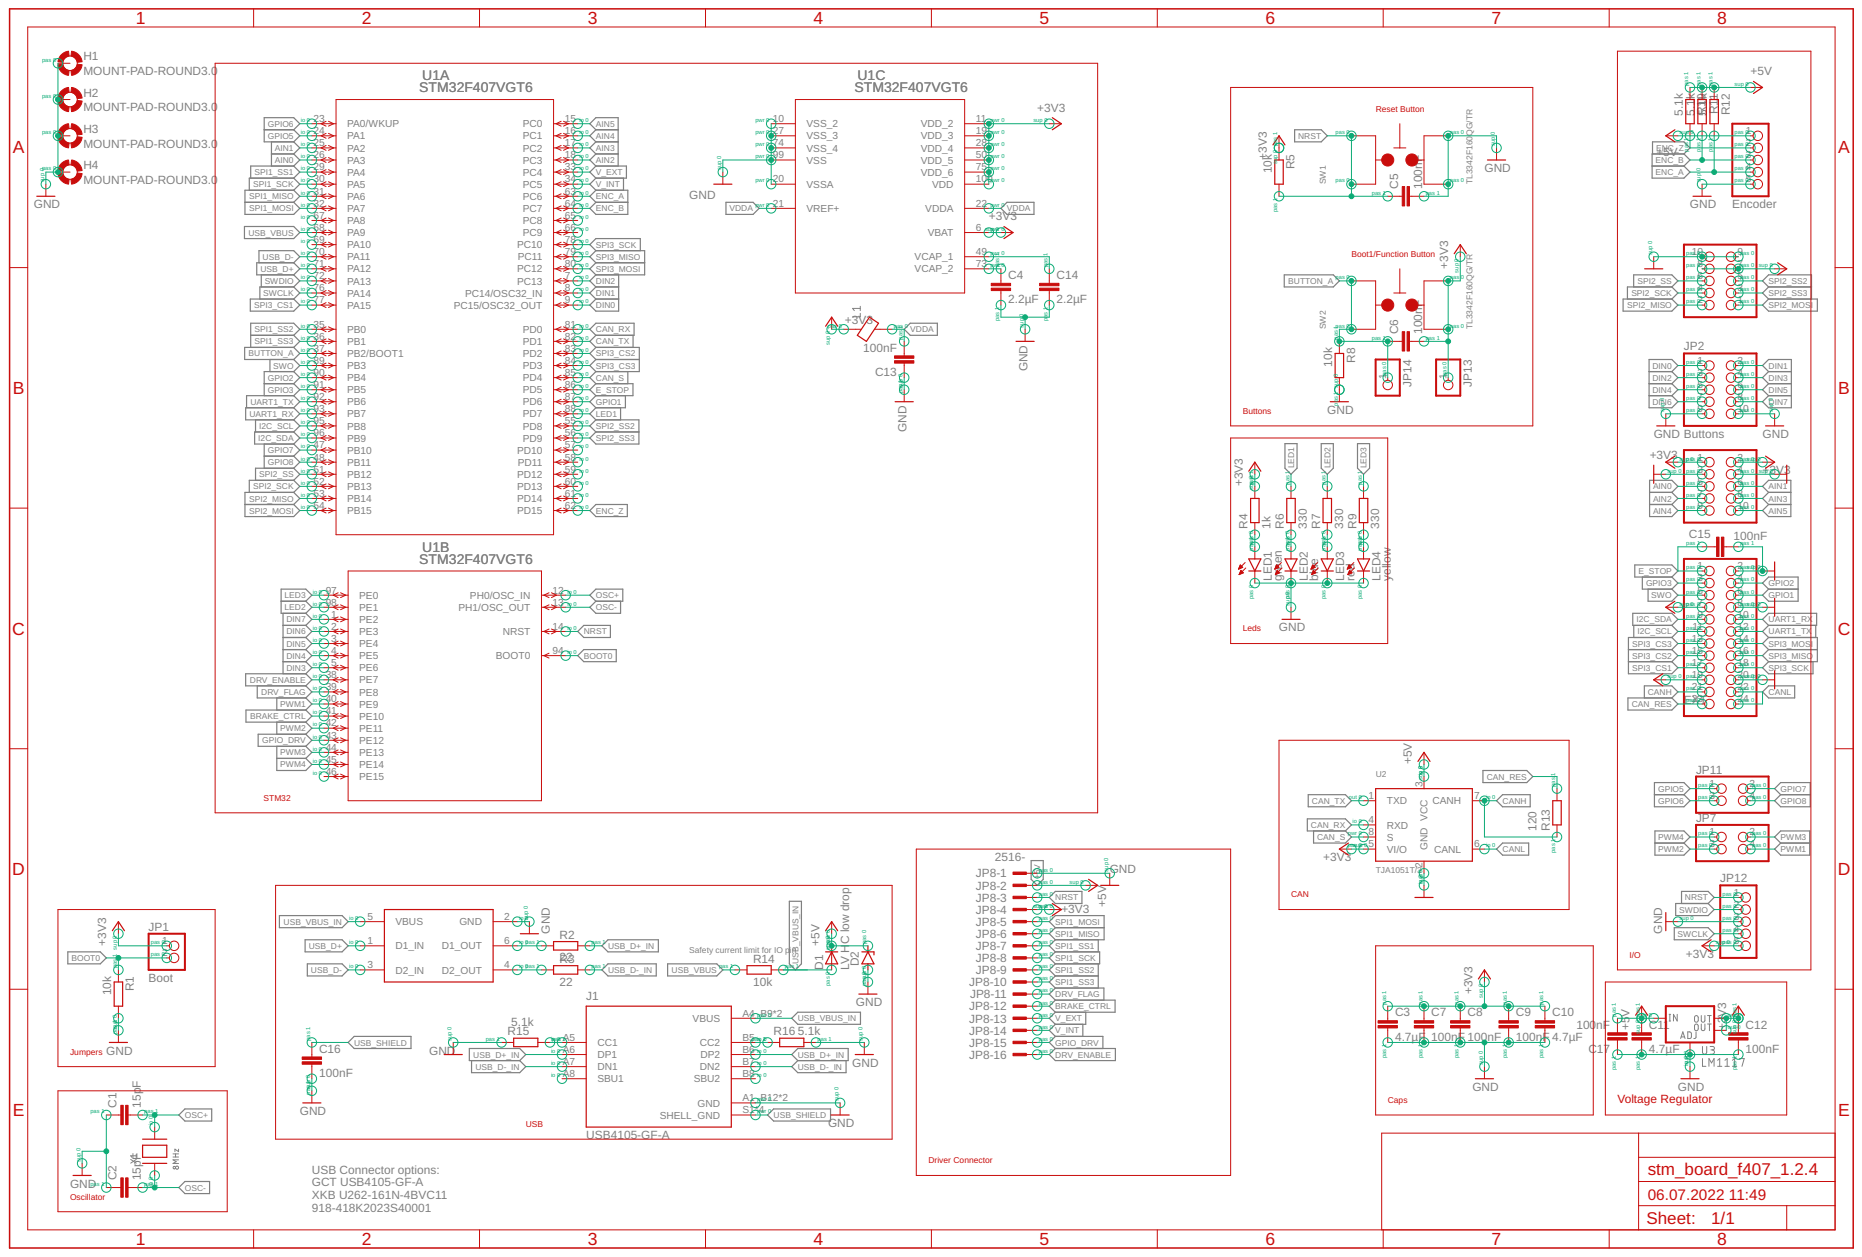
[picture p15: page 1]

SPI2_SS | SPI2_SS2
SPI2_SCK | SPI2_SS3
SPI2_MISO | SPI2_MOSI

DIN2 | DIN3
DIN4 | DIN5
DIN6 | DIN7

pas 0 pas 0 pas 1 pas 1

5 6 pas 0 pas 0

AIN0 | AIN1
AIN2 | AIN3

LV HC low drop +5V

sup 0 sup 0 pas 1 pas 1

Safety current limit for IO pin

spas 1 pas 1 pas 1 pas 1

USB Connector options: GCT USB4105-GF-A

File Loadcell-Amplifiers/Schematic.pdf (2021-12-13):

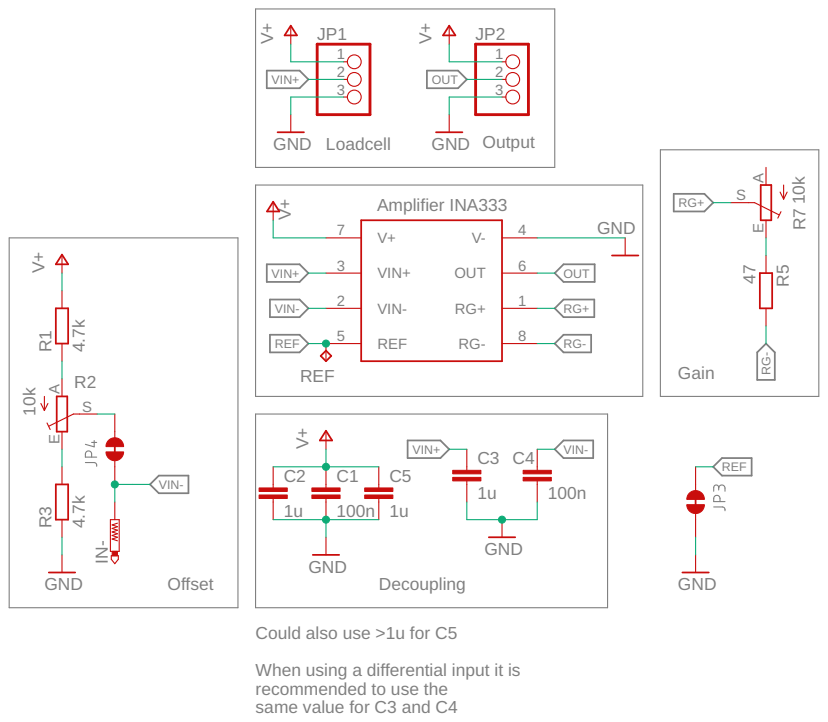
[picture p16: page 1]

Could also use >1u for C5

When using a differential input it is
recommended to use the
same value for C3 and C4

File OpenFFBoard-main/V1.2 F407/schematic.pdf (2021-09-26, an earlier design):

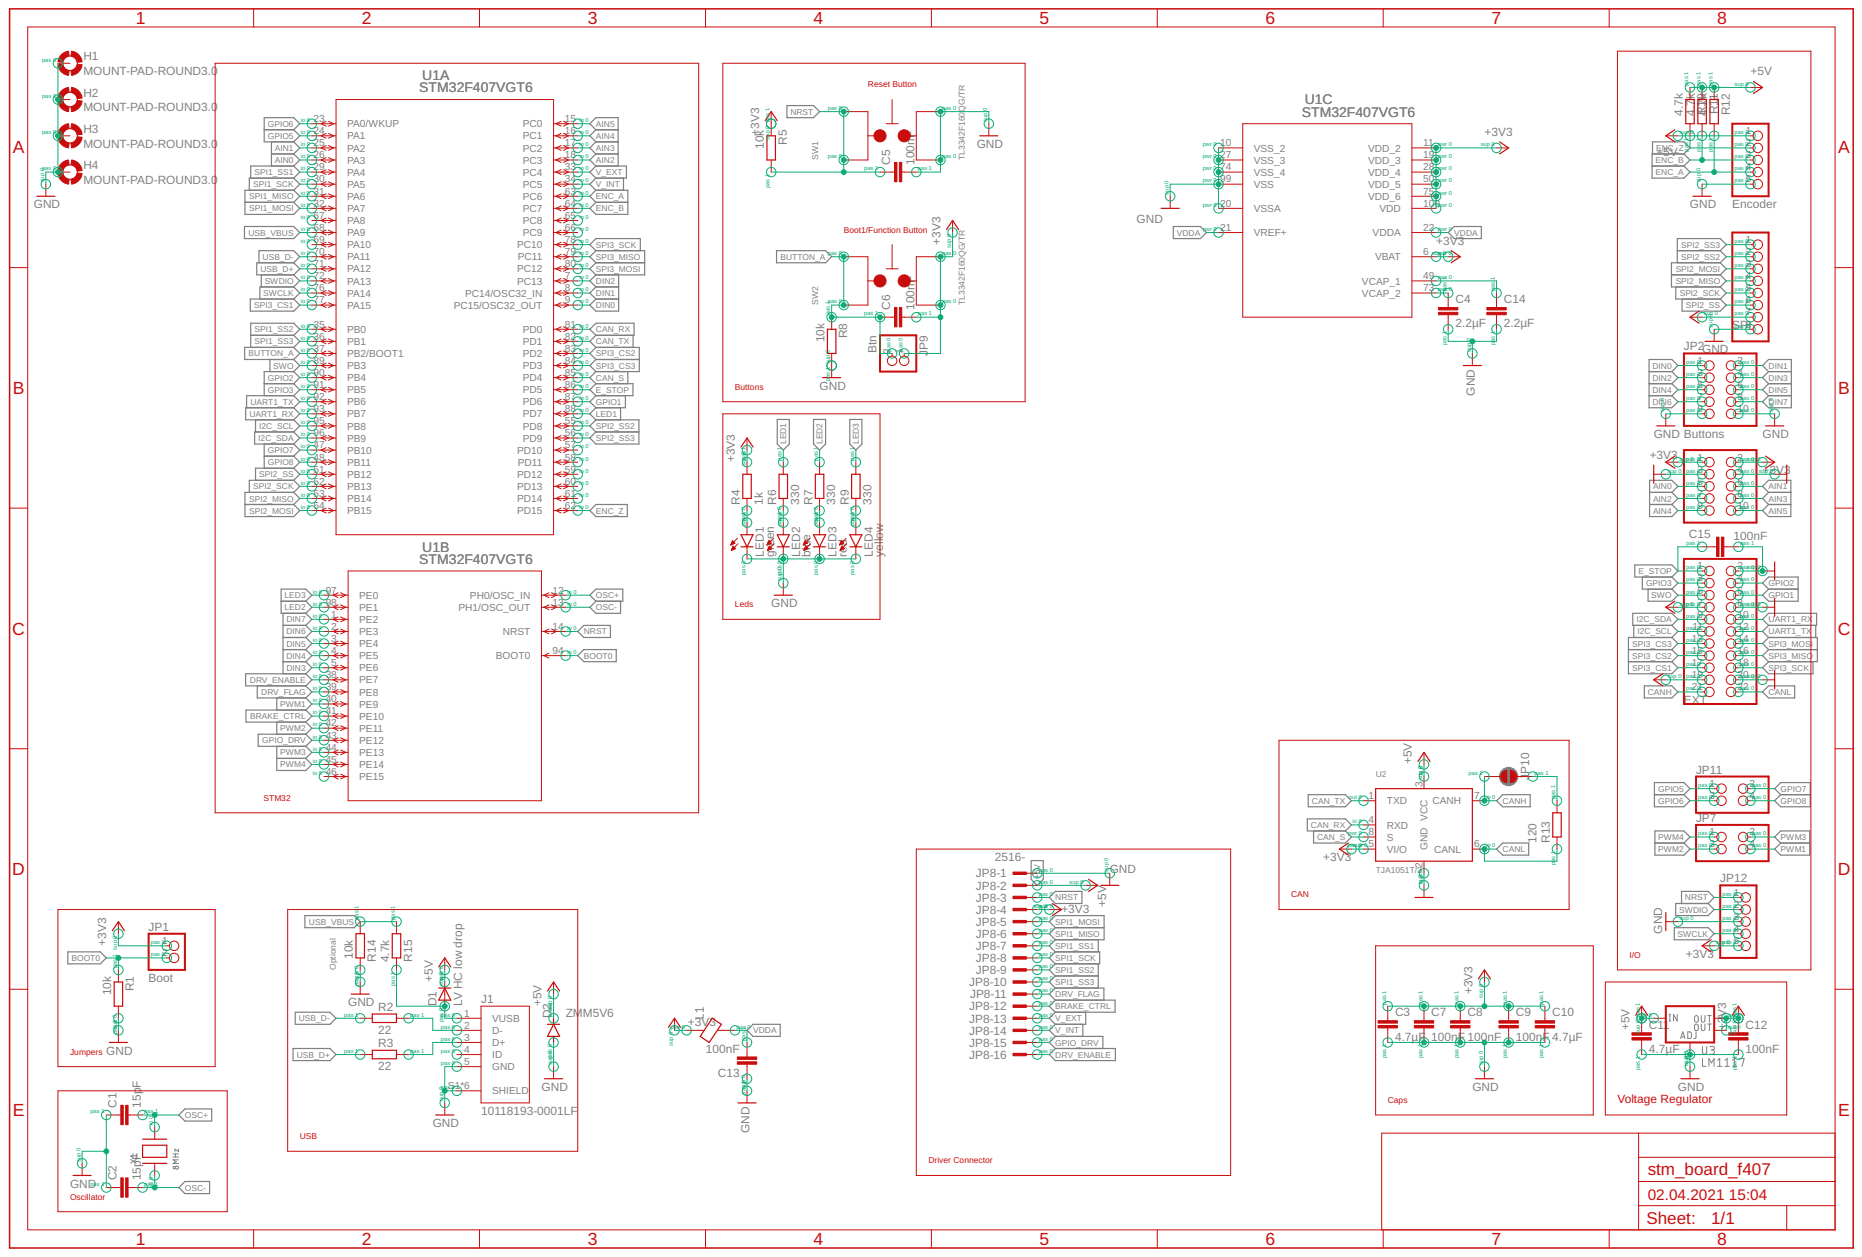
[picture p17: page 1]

pas 0 pas 0 pas 1 pas 1

sup 0 sup 0 pas 1 pas 1

LV HC low drop +5V

sup 0 pas 0 pas 0 sup 0

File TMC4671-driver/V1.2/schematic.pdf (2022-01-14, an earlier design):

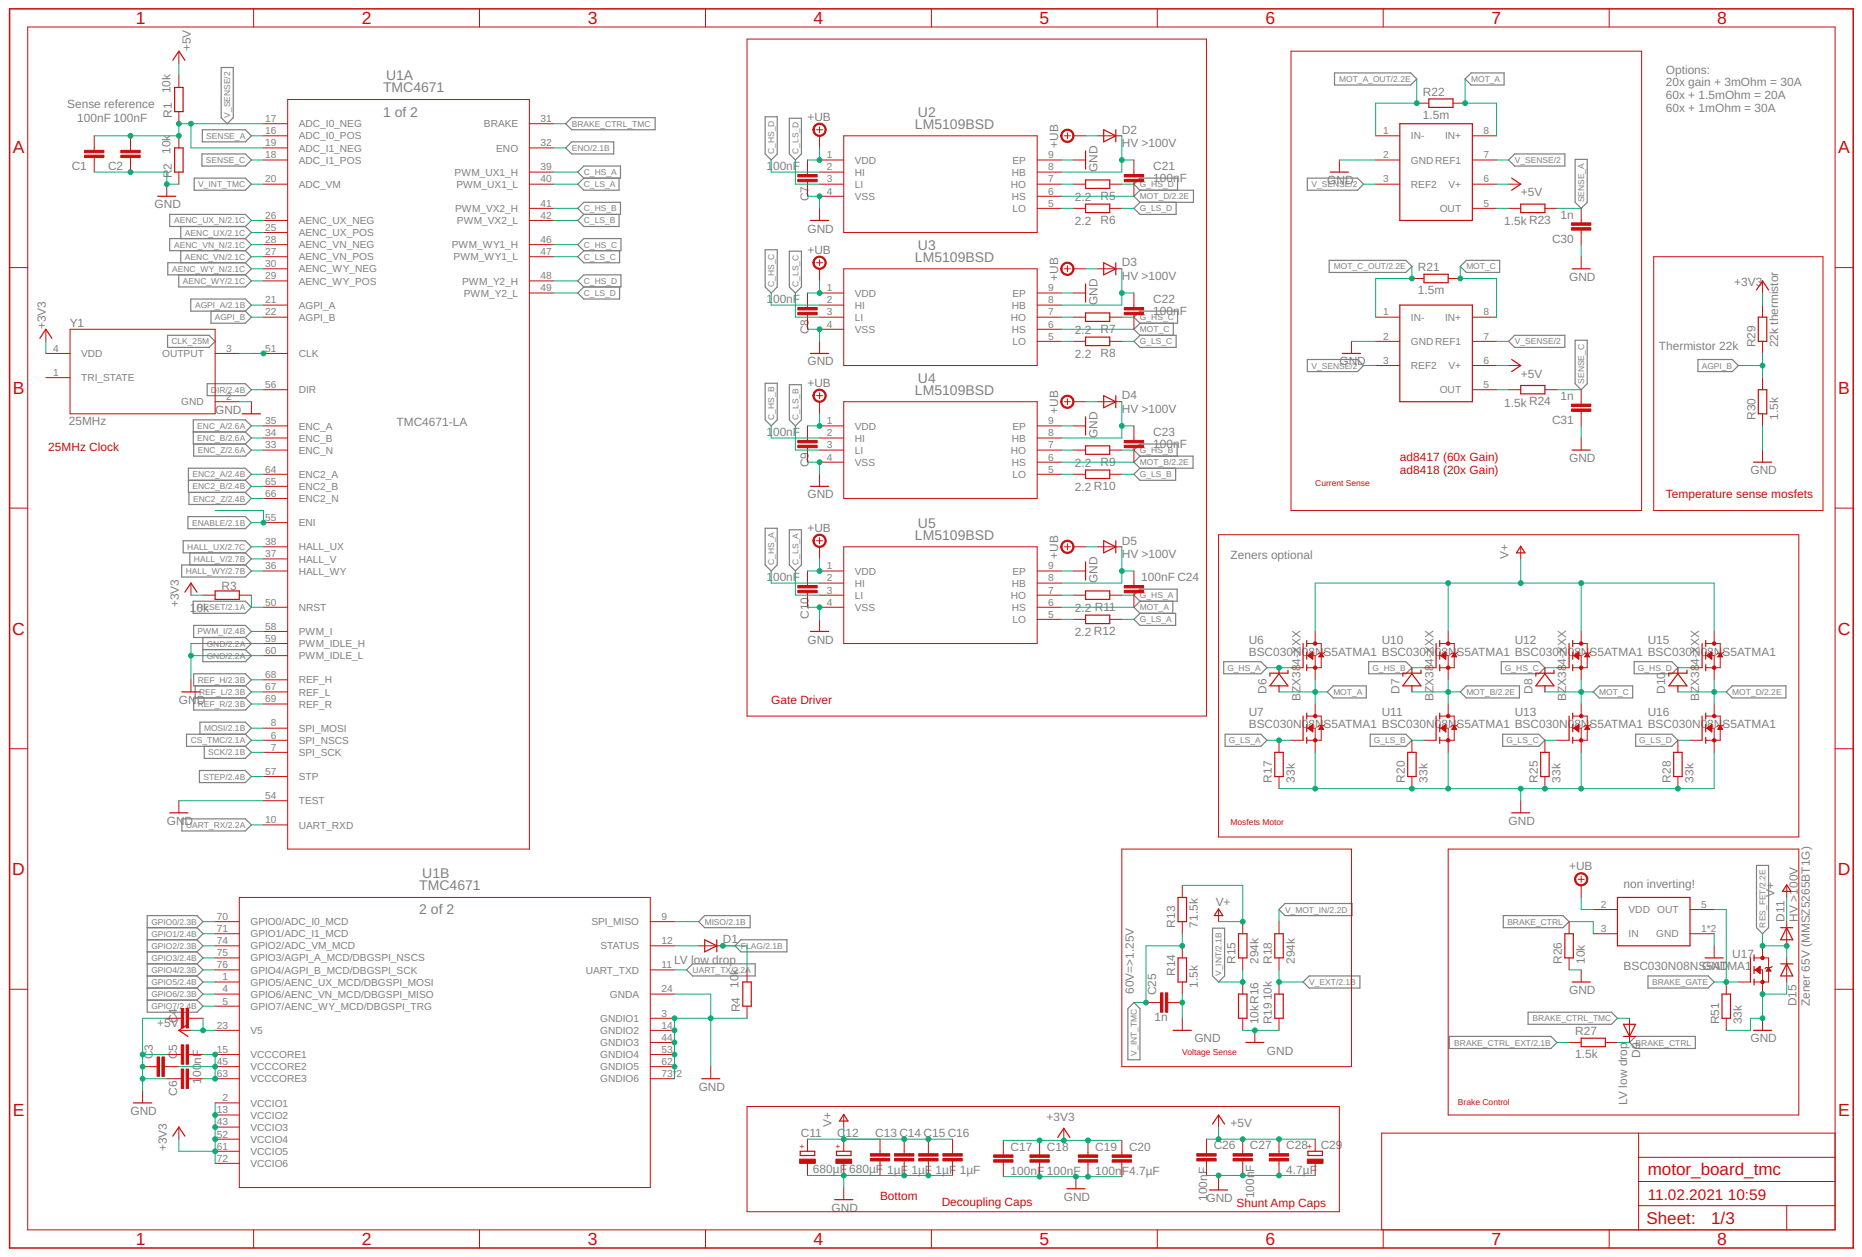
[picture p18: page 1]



Low ESR output cap. See MAX5033 Datasheet for selection info. Must have good input decoupling BSC030N08NS5ATM

https://datasheets.maximintegrated.com/en/ds/MAX5033.pdf
MAX5033

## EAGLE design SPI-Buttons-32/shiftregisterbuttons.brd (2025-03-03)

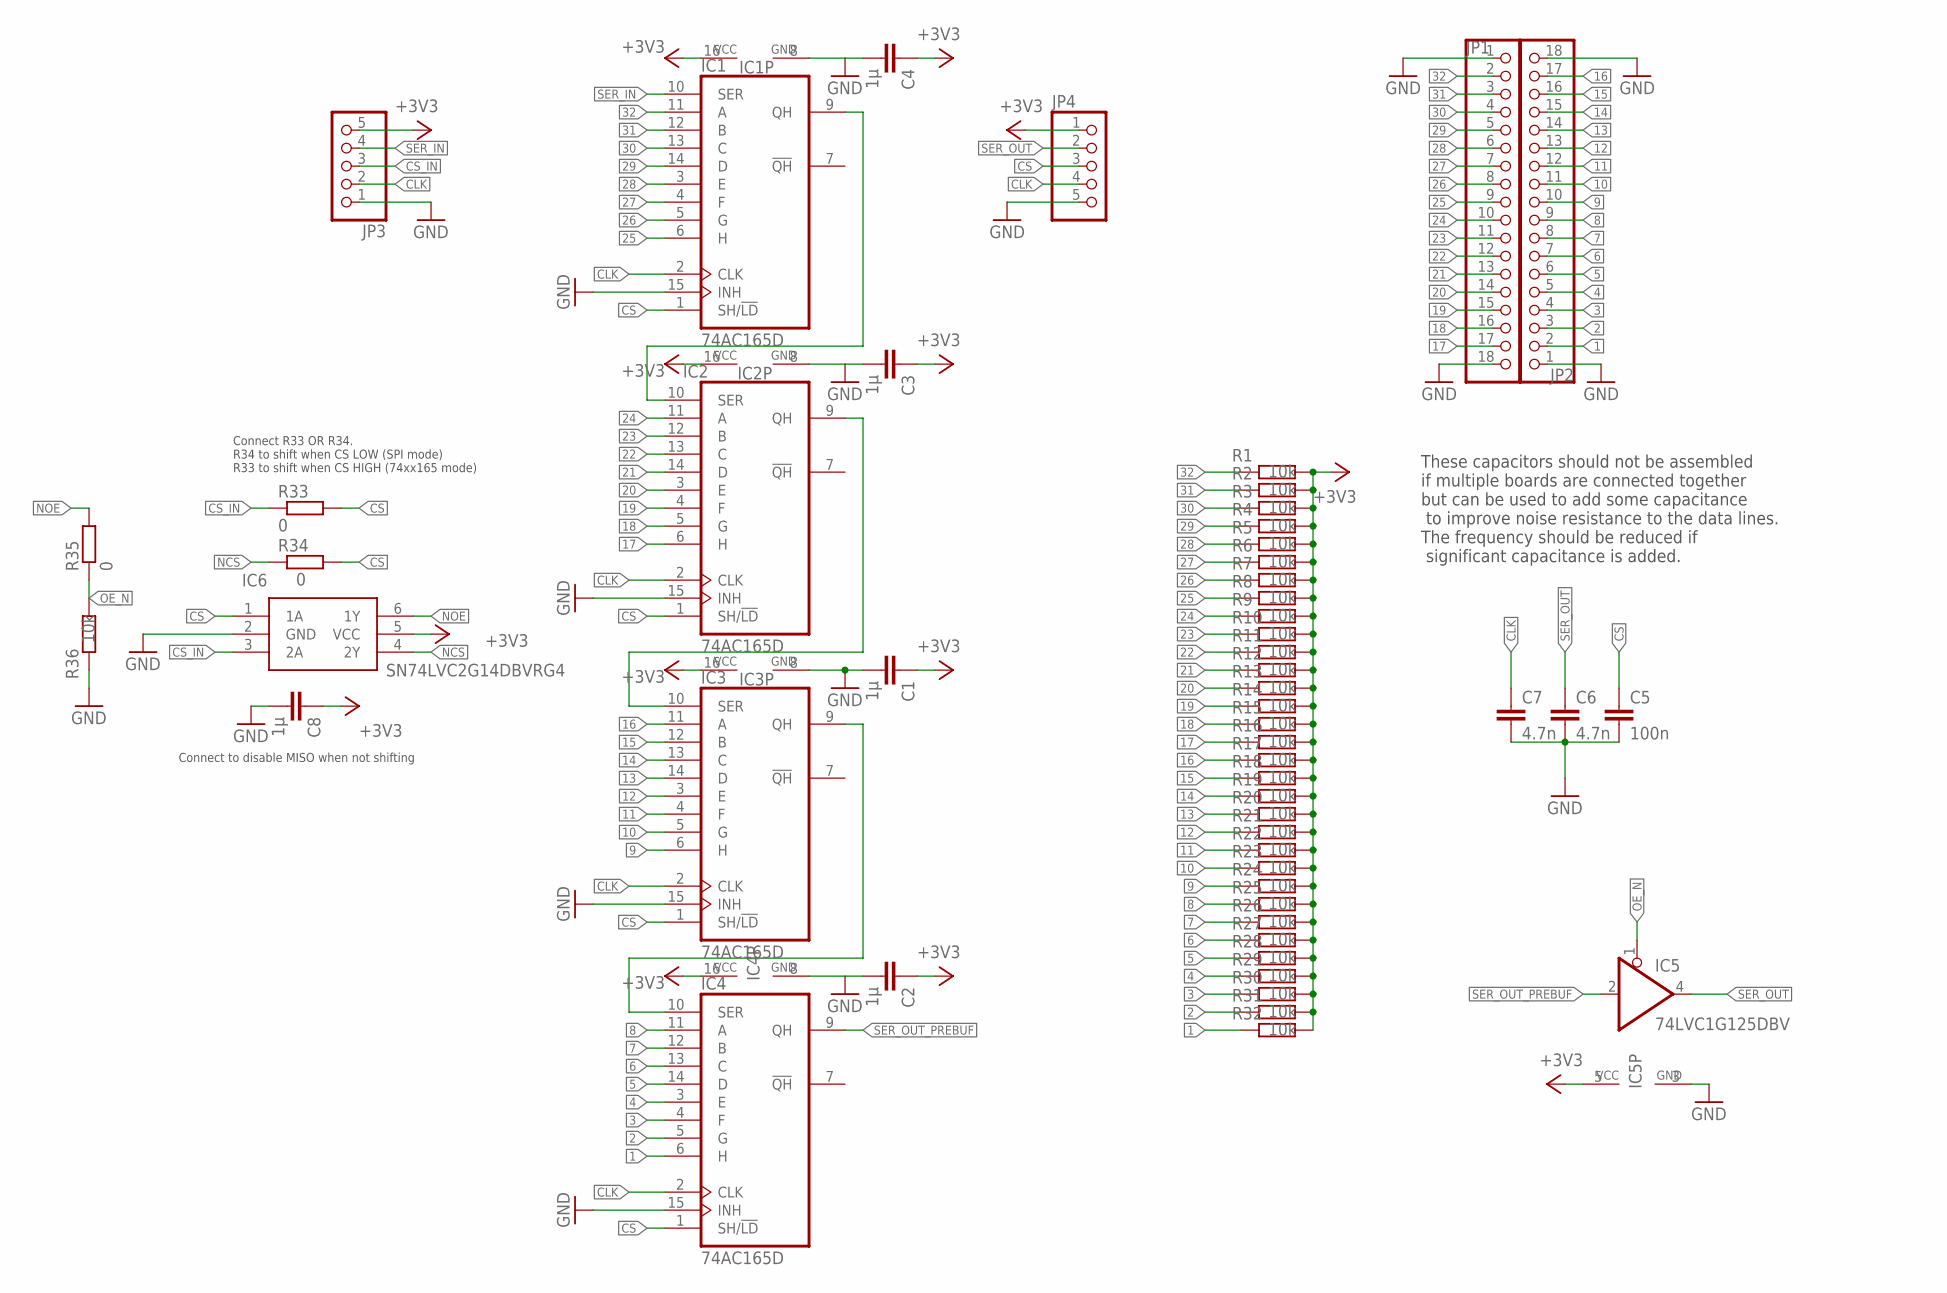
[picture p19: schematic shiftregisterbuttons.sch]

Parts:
C1, C2, C3, C4, C8: 1µ; C0603
C5: 100n; C0603
C6, C7: 4.7n; C0603
IC1, IC2, IC3, IC4: 74AC165D; SO16
IC5: 74LVC1G125DBV; SOT23-5
IC6: SN74LVC2G14DBVRG4; SOT95P280X145-6N
JP1, JP2: PINHD-1X18; 1X18
JP3, JP4: PINHD-1X5; 1X05
R1, R2, R3, R4, R5, R6, R7, R8, R9, R10, R11, R12, R13, R14, R15, R16, R17, R18, R19, R20, R21, R22, R23, R24, R25, R26, R27, R28, R29, R30, R31, R32, R36: 10k; R0603
R33, R34, R35: 0; R0603

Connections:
1: IC4.6 (H), JP2.2, R32.1
2: IC4.5 (G), JP2.3, R31.1
3: IC4.4 (F), JP2.4, R30.1
4: IC4.3 (E), JP2.5, R29.1
5: IC4.14 (D), JP2.6, R28.1
6: IC4.13 (C), JP2.7, R27.1
7: IC4.12 (B), JP2.8, R26.1
8: IC4.11 (A), JP2.9, R25.1
9: IC3.6 (H), JP2.10, R24.1
10: IC3.5 (G), JP2.11, R23.1
11: IC3.4 (F), JP2.12, R22.1
12: IC3.3 (E), JP2.13, R21.1
13: IC3.14 (D), JP2.14, R20.1
14: IC3.13 (C), JP2.15, R19.1
15: IC3.12 (B), JP2.16, R18.1
16: IC3.11 (A), JP2.17, R17.1
17: IC2.6 (H), JP1.17, R16.1
18: IC2.5 (G), JP1.16, R15.1
19: IC2.4 (F), JP1.15, R14.1
20: IC2.3 (E), JP1.14, R13.1
21: IC2.14 (D), JP1.13, R12.1
22: IC2.13 (C), JP1.12, R11.1
23: IC2.12 (B), JP1.11, R10.1
24: IC2.11 (A), JP1.10, R9.1
25: IC1.6 (H), JP1.9, R8.1
26: IC1.5 (G), JP1.8, R7.1
27: IC1.4 (F), JP1.7, R6.1
28: IC1.3 (E), JP1.6, R5.1
29: IC1.14 (D), JP1.5, R4.1
30: IC1.13 (C), JP1.4, R3.1
31: IC1.12 (B), JP1.3, R2.1
32: IC1.11 (A), JP1.2, R1.1
+3V3: C1.1, C2.1, C3.1, C4.1, C8.1, IC1.16 (VCC), IC2.16 (VCC), IC3.16 (VCC), IC4.16 (VCC), IC5.5 (VCC), IC6.5 (VCC), JP3.5, JP4.1, R1.2, R2.2, R3.2, R4.2, R5.2, R6.2, R7.2, R8.2, R9.2, R10.2, R11.2, R12.2, R13.2, R14.2, R15.2, R16.2, R17.2, R18.2, R19.2, R20.2, R21.2, R22.2, R23.2, R24.2, R25.2, R26.2, R27.2, R28.2, R29.2, R30.2, R31.2, R32.2
CLK: C7.1, IC1.2 (CLK), IC2.2 (CLK), IC3.2 (CLK), IC4.2 (CLK), JP3.2, JP4.4
CS: C5.1, IC1.1 (SH/!LD), IC2.1 (SH/!LD), IC3.1 (SH/!LD), IC4.1 (SH/!LD), IC6.1 (1A), JP4.3, R33.2, R34.2
CS_IN: IC6.3 (2A), JP3.3, R33.1
GND: C1.2, C2.2, C3.2, C4.2, C5.2, C6.2, C7.2, C8.2, IC1.8 (GND), IC1.15 (INH), IC2.8 (GND), IC2.15 (INH), IC3.8 (GND), IC3.15 (INH), IC4.8 (GND), IC4.15 (INH), IC5.3 (GND), IC6.2 (GND), JP1.1, JP1.18, JP2.1, JP2.18, JP3.1, JP4.5, R36.1
unnamed: IC2.9 (QH), IC3.10 (SER)
unnamed: IC3.9 (QH), IC4.10 (SER)
NCS: IC6.4 (2Y), R34.1
NOE: IC6.6 (1Y), R35.2
OE_N: IC5.1 (OE), R35.1, R36.2
SER1: IC1.9 (QH), IC2.10 (SER)
SER_IN: IC1.10 (SER), JP3.4
SER_OUT: C6.1, IC5.4 (O), JP4.2
SER_OUT_PREBUF: IC4.9 (QH), IC5.2 (I)

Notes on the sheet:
These capacitors should not be assembled if multiple boards are connected together but can be used to add some capacitance to improve noise resistance to the data lines. The frequency should be reduced if significant capacitance is added.
Connect to disable MISO when not shifting
Connect R33 OR R34. R34 to shift when CS LOW (SPI mode) R33 to shift when CS HIGH (74xx165 mode)

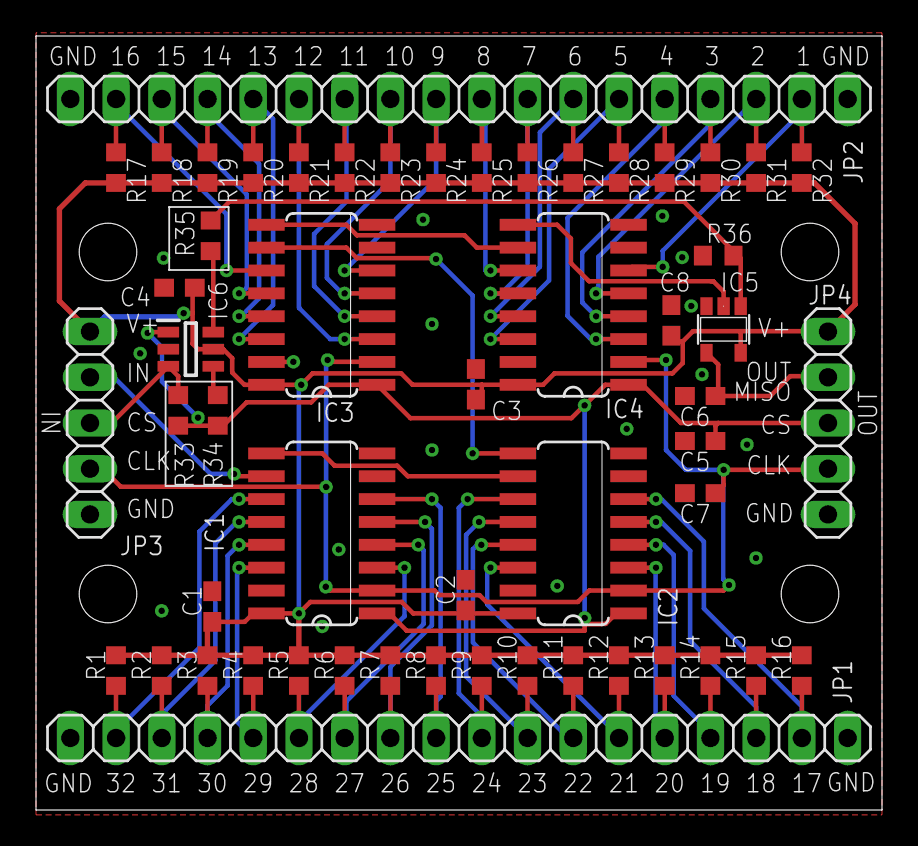
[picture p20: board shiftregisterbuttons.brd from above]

Board: 2 copper layers, 47.0 x 43.0 mm, 54 parts (0 on the bottom side), 46 nets.

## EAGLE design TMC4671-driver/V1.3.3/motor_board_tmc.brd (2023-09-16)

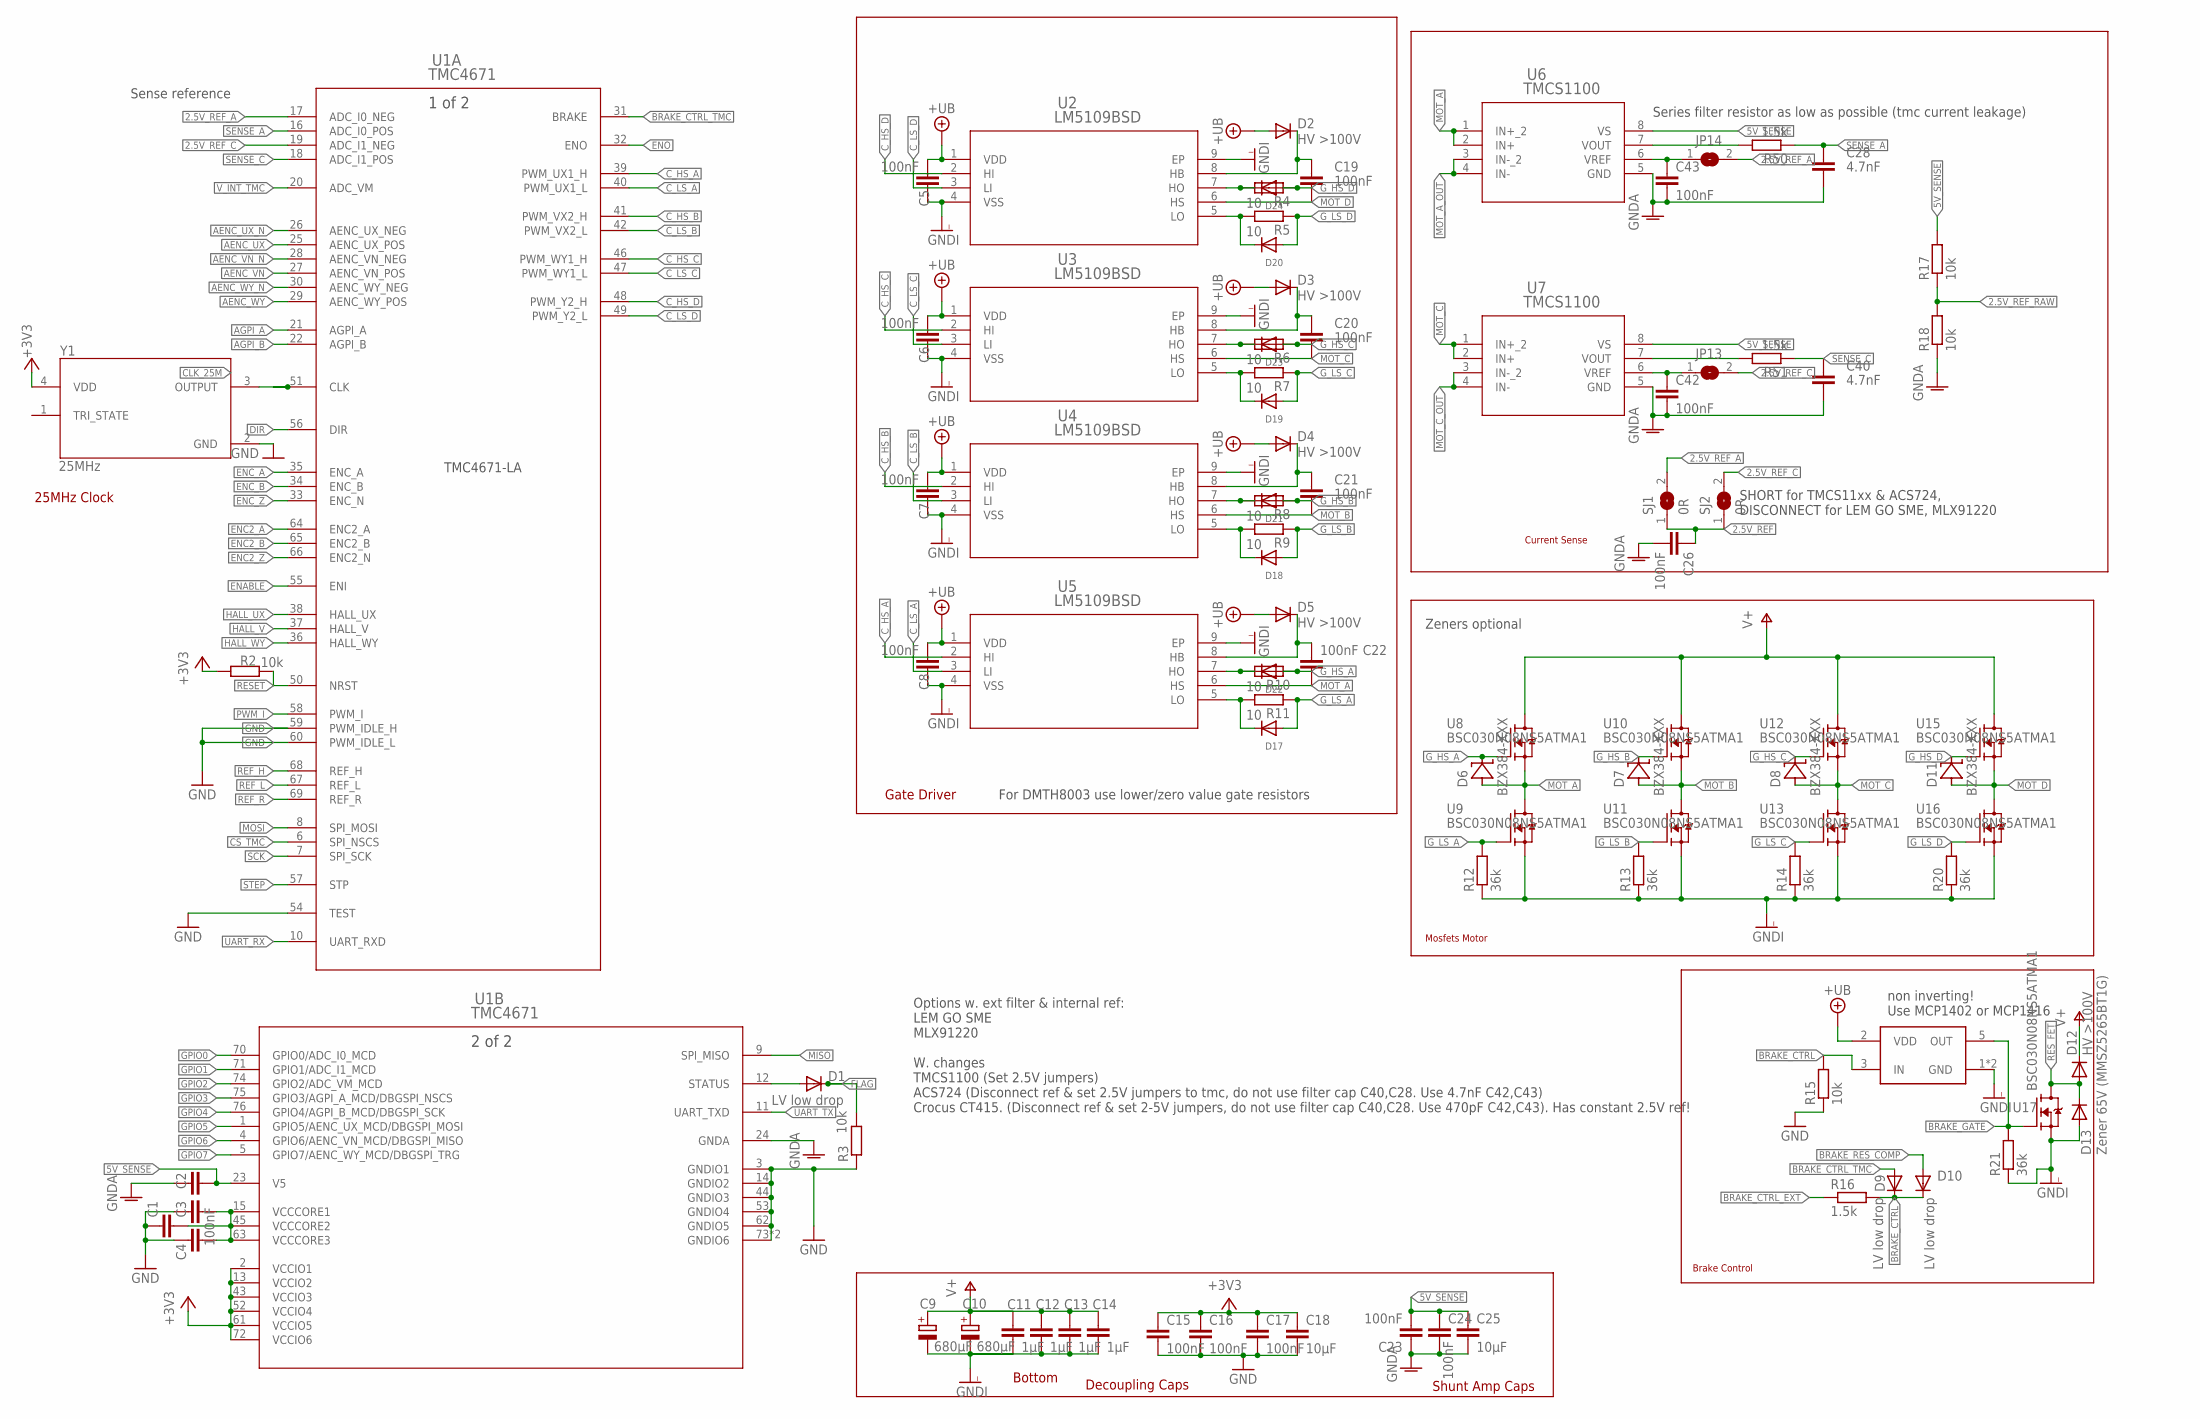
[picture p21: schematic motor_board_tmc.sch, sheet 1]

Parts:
C1, C3, C4, C5, C6, C7, C8, C15, C16, C17, C19, C20, C21, C22, C23, C24, C26, C42, C43: 100nF; C0603
C2, C18, C25: 10µF; C0805
C9, C10: 680µF; E7,5-16
C11, C12, C13, C14: 1µF; C1206
C28, C40: 4.7nF; C0603
D1, D9, D10: LV low drop; SOD-123FL
D2, D3, D4, D5, D12: HV >100V; SOD-123FL
D6, D7, D8, D11: BZX384-XXX; SOD323-R
D13: Zener 65V (MMSZ5265BT1G); SOD-123FL
D17, D18, D19, D20, D21, D22, D23, D24: DIODESOD-323F; SOD-323F
JP13, JP14: JUMPER-SMT_2_NO_SILK; RESISTOR_R0603
R2, R3, R15, R17, R18: 10k; R0603
R4, R5, R6, R7, R8, R9, R10, R11: 10; R0603
R12, R13, R14, R20, R21: 36k; R0603
R16, R50, R51: 1.5k; R0603
SJ1, SJ2: 0R; RESISTOR_R0603
U1: TMC4671; QFN76_10P5X6P5
U2, U3, U4, U5: LM5109BSD; SDC08A
U6, U7: TMCS1100; SOIC8_D_TEX
U8, U9, U10, U11, U12, U13, U15, U16, U17: BSC030N08NS5ATMA1; MOSFET_BSC093N04LSGATMA1
U14: MCP14XX; SOT23-5L
Y1: 25MHz; ECS-327KE-TR

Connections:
2.5V_REF: C26.1, SJ1.1, SJ2.1; also elsewhere on the board
2.5V_REF_A: JP14.2, SJ1.2, U1.17 (ADC_I0_NEG)
2.5V_REF_C: JP13.2, SJ2.2, U1.19 (ADC_I1_NEG)
2.5V_REF_RAW: R17.1, R18.2; also elsewhere on the board
5V_SENSE: C2.2, C23.2, C24.1, C25.1, R17.2, U1.23 (V5), U6.8 (VS), U7.8 (VS); also elsewhere on the board
+3V3: C15.1, C16.1, C17.1, C18.1, R2.2, U1.2 (VCCIO1), U1.13 (VCCIO2), U1.43 (VCCIO3), U1.52 (VCCIO4), U1.61 (VCCIO5), U1.72 (VCCIO6), Y1.4 (VDD); also elsewhere on the board
AENC_UX: U1.25 (AENC_UX_POS); also elsewhere on the board
AENC_UX_N: U1.26 (AENC_UX_NEG); also elsewhere on the board
AENC_VN: U1.27 (AENC_VN_POS); also elsewhere on the board
AENC_VN_N: U1.28 (AENC_VN_NEG); also elsewhere on the board
AENC_WY: U1.29 (AENC_WY_POS); also elsewhere on the board
AENC_WY_N: U1.30 (AENC_WY_NEG); also elsewhere on the board
AGPI_A: U1.21 (AGPI_A); also elsewhere on the board
AGPI_B: U1.22 (AGPI_B); also elsewhere on the board
BRAKE_CTRL: D9.C, D10.C, R15.2, R16.2, U14.3 (IN)
BRAKE_CTRL_EXT: R16.1; also elsewhere on the board
BRAKE_CTRL_TMC: D9.A, U1.31 (BRAKE)
BRAKE_GATE: R21.2, U14.5 (OUT), U17.4 (G)
BRAKE_RES_COMP: D10.A; also elsewhere on the board
CLK_25M: U1.51 (CLK), Y1.3 (OUTPUT)
CS_TMC: U1.6 (SPI_NSCS); also elsewhere on the board
C_HS_A: U1.39 (PWM_UX1_H), U5.2 (HI)
C_HS_B: U1.41 (PWM_VX2_H), U4.2 (HI)
C_HS_C: U1.46 (PWM_WY1_H), U3.2 (HI)
C_HS_D: U1.48 (PWM_Y2_H), U2.2 (HI)
C_LS_A: U1.40 (PWM_UX1_L), U5.3 (LI)
C_LS_B: U1.42 (PWM_VX2_L), U4.3 (LI)
C_LS_C: U1.47 (PWM_WY1_L), U3.3 (LI)
C_LS_D: U1.49 (PWM_Y2_L), U2.3 (LI)
DIR: U1.56 (DIR); also elsewhere on the board
ENABLE: U1.55 (ENI); also elsewhere on the board
ENC2_A: U1.64 (ENC2_A); also elsewhere on the board
ENC2_B: U1.65 (ENC2_B); also elsewhere on the board
ENC2_Z: U1.66 (ENC2_N); also elsewhere on the board
ENC_A: U1.35 (ENC_A); also elsewhere on the board
ENC_B: U1.34 (ENC_B); also elsewhere on the board
ENC_Z: U1.33 (ENC_N); also elsewhere on the board
ENO: U1.32 (ENO); also elsewhere on the board
FLAG: D1.C, R3.2; also elsewhere on the board
GND: C1.1, C3.1, C4.1, C15.2, C16.2, C17.2, C18.2, R3.1, R15.1, U1.3 (GNDIO1), U1.14 (GNDIO2), U1.44 (GNDIO3), U1.53 (GNDIO4), U1.54 (TEST), U1.59 (PWM_IDLE_H), U1.60 (PWM_IDLE_L), U1.62 (GNDIO5), U1.73 (GNDIO6), U1.77 (GNDIO6), Y1.2 (GND); also elsewhere on the board
GNDA: C2.1, C23.1, C24.2, C25.2, C26.2, C28.2, C40.2, C42.2, C43.2, R18.1, U1.24 (GNDA), U6.5 (GND), U7.5 (GND); also elsewhere on the board
GNDI: C5.1, C6.1, C7.1, C8.1, C9.-, C10.-, C11.2, C12.2, C13.2, C14.2, D13.A, R12.1, R13.1, R14.1, R20.1, R21.1, U2.4 (VSS), U2.9 (EP), U3.4 (VSS), U3.9 (EP), U4.4 (VSS), U4.9 (EP), U5.4 (VSS), U5.9 (EP), U9.1 (S), U9.2 (S), U9.3 (S), U11.1 (S), U11.2 (S), U11.3 (S), U13.1 (S), U13.2 (S), U13.3 (S), U14.1 (GND), U14.4 (GND), U16.1 (S), U16.2 (S), U16.3 (S), U17.1 (S), U17.2 (S), U17.3 (S); also elsewhere on the board
GPIO0: U1.70 (GPIO0/ADC_I0_MCD); also elsewhere on the board
GPIO1: U1.71 (GPIO1/ADC_I1_MCD); also elsewhere on the board
GPIO2: U1.74 (GPIO2/ADC_VM_MCD); also elsewhere on the board
GPIO3: U1.75 (GPIO3/AGPI_A_MCD/DBGSPI_NSCS); also elsewhere on the board
GPIO4: U1.76 (GPIO4/AGPI_B_MCD/DBGSPI_SCK); also elsewhere on the board
GPIO5: U1.1 (GPIO5/AENC_UX_MCD/DBGSPI_MOSI); also elsewhere on the board
GPIO6: U1.4 (GPIO6/AENC_VN_MCD/DBGSPI_MISO); also elsewhere on the board
GPIO7: U1.5 (GPIO7/AENC_WY_MCD/DBGSPI_TRG); also elsewhere on the board
G_HS_A: D6.C, D22.A, R10.1, U8.4 (G)
G_HS_B: D7.C, D21.A, R8.1, U10.4 (G)
G_HS_C: D8.C, D23.A, R6.1, U12.4 (G)
G_HS_D: D11.C, D24.A, R4.1, U15.4 (G)
G_LS_A: D17.A, R11.1, R12.2, U9.4 (G)
G_LS_B: D18.A, R9.1, R13.2, U11.4 (G)
G_LS_C: D19.A, R7.1, R14.2, U13.4 (G)
G_LS_D: D20.A, R5.1, R20.2, U16.4 (G)
HALL_UX: U1.38 (HALL_UX); also elsewhere on the board
HALL_V: U1.37 (HALL_V); also elsewhere on the board
HALL_WY: U1.36 (HALL_WY); also elsewhere on the board
MISO: U1.9 (SPI_MISO); also elsewhere on the board
MOSI: U1.8 (SPI_MOSI); also elsewhere on the board
MOT_A: C22.2, D6.A, U5.6 (HS), U6.1 (IN+_2), U6.2 (IN+), U8.1 (S), U8.2 (S), U8.3 (S), U9.5 (D)
MOT_A_OUT: U6.3 (IN-_2), U6.4 (IN-); also elsewhere on the board
MOT_B: C21.2, D7.A, U4.6 (HS), U10.1 (S), U10.2 (S), U10.3 (S), U11.5 (D); also elsewhere on the board
MOT_C: C20.2, D8.A, U3.6 (HS), U7.1 (IN+_2), U7.2 (IN+), U12.1 (S), U12.2 (S), U12.3 (S), U13.5 (D)
MOT_C_OUT: U7.3 (IN-_2), U7.4 (IN-); also elsewhere on the board
MOT_D: C19.2, D11.A, U2.6 (HS), U15.1 (S), U15.2 (S), U15.3 (S), U16.5 (D); also elsewhere on the board
unnamed: D1.A, U1.12 (STATUS)
unnamed: D17.C, R11.2, U5.5 (LO)
unnamed: C22.1, D5.C, U5.8 (HB)
unnamed: D22.C, R10.2, U5.7 (HO)
unnamed: C21.1, D4.C, U4.8 (HB)
unnamed: D18.C, R9.2, U4.5 (LO)
unnamed: D21.C, R8.2, U4.7 (HO)
unnamed: C19.1, D2.C, U2.8 (HB)
unnamed: D20.C, R5.2, U2.5 (LO)
unnamed: D24.C, R4.2, U2.7 (HO)
unnamed: C20.1, D3.C, U3.8 (HB)
unnamed: D19.C, R7.2, U3.5 (LO)
unnamed: D23.C, R6.2, U3.7 (HO)
PWM_I: U1.58 (PWM_I); also elsewhere on the board
REF_H: U1.68 (REF_H); also elsewhere on the board
REF_L: U1.67 (REF_L); also elsewhere on the board
REF_R: U1.69 (REF_R); also elsewhere on the board
RESET: R2.1, U1.50 (NRST); also elsewhere on the board
RES_FET: D12.A, D13.C, U17.5 (D); also elsewhere on the board
SCK: U1.7 (SPI_SCK); also elsewhere on the board
SENSE_A: C28.1, R50.1, U1.16 (ADC_I0_POS)
SENSE_A_RAW: R50.2, U6.7 (VOUT)
SENSE_C: C40.1, R51.1, U1.18 (ADC_I1_POS)
SENSE_C_RAW: R51.2, U7.7 (VOUT)
STEP: U1.57 (STP); also elsewhere on the board
UART_RX: U1.10 (UART_RXD); also elsewhere on the board
UART_TX: U1.11 (UART_TXD); also elsewhere on the board
V+: C9.+, C10.+, C11.1, C12.1, C13.1, C14.1, D12.C, U8.5 (D), U10.5 (D), U12.5 (D), U15.5 (D); also elsewhere on the board
VCORE: C1.2, C3.2, C4.2, U1.15 (VCCCORE1), U1.45 (VCCCORE2), U1.63 (VCCCORE3)
VREF_A_RAW: C43.1, JP14.1, U6.6 (VREF)
VREF_C_RAW: C42.1, JP13.1, U7.6 (VREF)
V_GD: C5.2, C6.2, C7.2, C8.2, D2.A, D3.A, D4.A, D5.A, U2.1 (VDD), U3.1 (VDD), U4.1 (VDD), U5.1 (VDD), U14.2 (VDD); also elsewhere on the board
V_INT_TMC: U1.20 (ADC_VM); also elsewhere on the board

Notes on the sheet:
Mosfets Motor
Gate Driver
Current Sense
Brake Control
Shunt Amp Caps
Decoupling Caps
25MHz Clock
Bottom
Sense reference
Zeners optional
TMC4671-LA
non inverting! Use MCP1402 or MCP1416
SHORT for TMCS11xx & ACS724, DISCONNECT for LEM GO SME, MLX91220
Options w. ext filter & internal ref: LEM GO SME MLX91220 W. changes TMCS1100 (Set 2.5V jumpers) ACS724 (Disconnect ref & set 2.5V jumpers to tmc, do not use filter cap C40,C28. Use 4.7nF C42,C43) Crocus CT415. (Disconnect ref & set 2-5V jumpers, do not use filter cap C40,C28. Use 470pF C42,C43). H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
Series filter resistor as low as possible (tmc current leakage)
For DMTH8003 use lower/zero value gate resistors

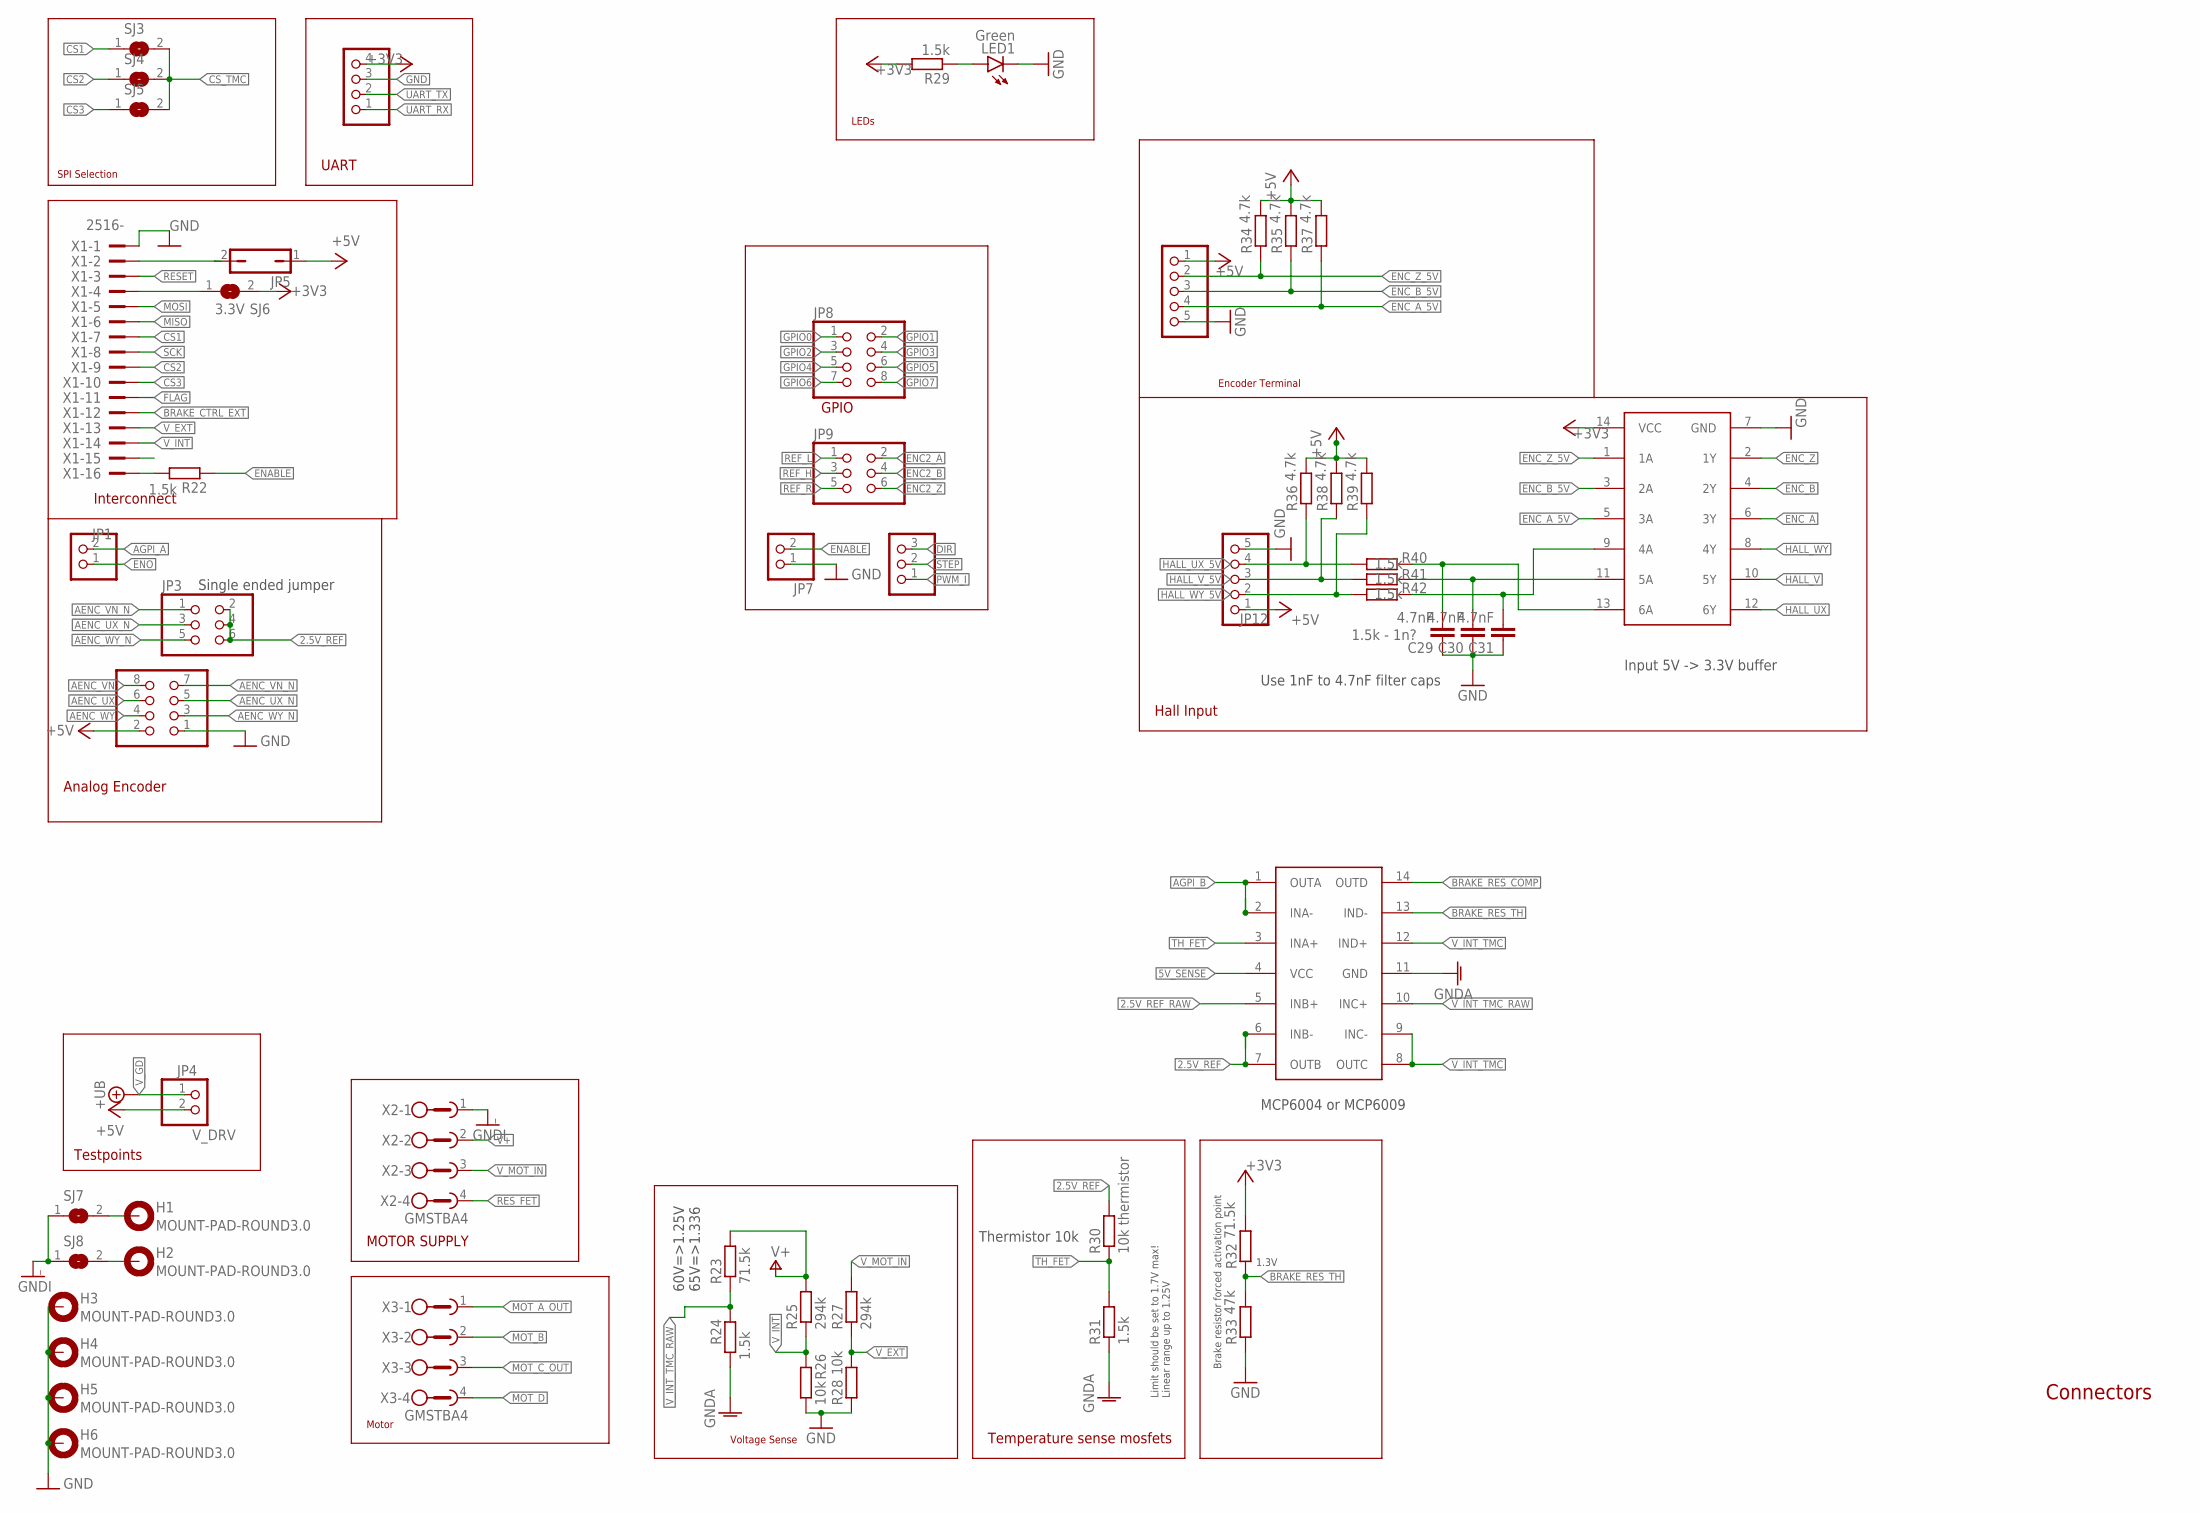
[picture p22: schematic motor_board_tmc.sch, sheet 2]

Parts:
C29, C30, C31: 4.7nF; C0603
H1, H2, H3, H4, H5, H6: MOUNT-PAD-ROUND3.0; 3,0-PAD
JP1, JP7: PINHD-1X2; 1X02
JP2, JP8: PINHD-2X4; 2X04
JP3, JP9: PINHD-2X3; 2X03
JP4: V_DRV; 1X02
JP5: JP1Q; JP1
JP6: PINHD-1X4; 1X04
JP10: PINHD-1X3; 1X03
JP11, JP12: PINHD-1X5; 1X05
LED1: Green; SML0805
R22, R24, R29, R31, R40, R41, R42: 1.5k; R0603
R23, R32: 71.5k; R0805
R25, R27: 294k; R0805
R26, R28: 10k; R0603
R30: 10k thermistor; R0603
R33: 47k; R0603
R34, R35, R36, R37, R38, R39: 4.7k; R0603
SJ3, SJ4, SJ5, SJ7, SJ8: SJ
SJ6: 3.3V; SJ
U18: MCP6004; TSSOP14
U19: 74LV17APWJ; TSSOP14
X1: 2516-; PAK100/2500-16
X2, X3: GMSTBA4

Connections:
2.5V_REF: JP3.2, JP3.4, JP3.6, R30.2, U18.6 (INB-), U18.7 (OUTB); also elsewhere on the board
2.5V_REF_RAW: U18.5 (INB+); also elsewhere on the board
5V_SENSE: U18.4 (VCC); also elsewhere on the board
+3V3: JP6.4, R29.2, R32.2, SJ6.2, U19.14 (VCC); also elsewhere on the board
+5V: JP2.2, JP4.2, JP5.1, JP11.1, JP12.1, R34.2, R35.2, R36.2, R37.2, R38.2, R39.2; also elsewhere on the board
AENC_UX: JP2.6; also elsewhere on the board
AENC_UX_N: JP2.5, JP3.3; also elsewhere on the board
AENC_VN: JP2.8; also elsewhere on the board
AENC_VN_N: JP2.7, JP3.1; also elsewhere on the board
AENC_WY: JP2.4; also elsewhere on the board
AENC_WY_N: JP2.3, JP3.5; also elsewhere on the board
AGPI_A: JP1.2; also elsewhere on the board
AGPI_B: U18.1 (OUTA), U18.2 (INA-); also elsewhere on the board
BRAKE_CTRL_EXT: X1.12; also elsewhere on the board
BRAKE_RES_COMP: U18.14 (OUTD); also elsewhere on the board
BRAKE_RES_TH: R32.1, R33.2, U18.13 (IND-)
CS1: SJ3.1, X1.7
CS2: SJ4.1, X1.9
CS3: SJ5.1, X1.10
CS_TMC: SJ3.2, SJ4.2, SJ5.2; also elsewhere on the board
DIR: JP10.3; also elsewhere on the board
ENABLE: JP7.2, R22.1; also elsewhere on the board
ENC2_A: JP9.2; also elsewhere on the board
ENC2_B: JP9.4; also elsewhere on the board
ENC2_Z: JP9.6; also elsewhere on the board
ENC_A: U19.6 (3Y); also elsewhere on the board
ENC_A_5V: JP11.4, R37.1, U19.5 (3A)
ENC_B: U19.4 (2Y); also elsewhere on the board
ENC_B_5V: JP11.3, R35.1, U19.3 (2A)
ENC_Z: U19.2 (1Y); also elsewhere on the board
ENC_Z_5V: JP11.2, R34.1, U19.1 (1A)
ENO: JP1.1; also elsewhere on the board
FLAG: X1.11; also elsewhere on the board
GND: C29.1, C30.1, C31.1, H3.B3,0, H4.B3,0, H5.B3,0, H6.B3,0, JP2.1, JP6.3, JP7.1, JP11.5, JP12.5, LED1.C, R26.1, R28.1, R33.1, U19.7 (GND), X1.1; also elsewhere on the board
GNDA: R24.1, R31.1, U18.11 (GND); also elsewhere on the board
GNDI: SJ7.1, SJ8.1, X2.1; also elsewhere on the board
GPIO0: JP8.1; also elsewhere on the board
GPIO1: JP8.2; also elsewhere on the board
GPIO2: JP8.3; also elsewhere on the board
GPIO3: JP8.4; also elsewhere on the board
GPIO4: JP8.5; also elsewhere on the board
GPIO5: JP8.6; also elsewhere on the board
GPIO6: JP8.7; also elsewhere on the board
GPIO7: JP8.8; also elsewhere on the board
HALL_UX: U19.12 (6Y); also elsewhere on the board
HALL_UX_5V: C29.2, R40.1, U19.13 (6A)
HALL_V: U19.10 (5Y); also elsewhere on the board
HALL_V_5V: C30.2, R41.1, U19.11 (5A)
HALL_WY: U19.8 (4Y); also elsewhere on the board
HALL_WY_5V: C31.2, R42.1, U19.9 (4A)
MISO: X1.6; also elsewhere on the board
MOSI: X1.5; also elsewhere on the board
MOT_A_OUT: X3.1; also elsewhere on the board
MOT_B: X3.2; also elsewhere on the board
MOT_C_OUT: X3.3; also elsewhere on the board
MOT_D: X3.4; also elsewhere on the board
unnamed: JP12.4, R36.1, R40.2
unnamed: JP12.3, R38.1, R41.2
unnamed: H1.B3,0, SJ7.2
unnamed: LED1.A, R29.1
unnamed: JP5.2, X1.2
unnamed: H2.B3,0, SJ8.2
unnamed: JP12.2, R39.1, R42.2
unnamed: R22.2, X1.16
unnamed: SJ6.1, X1.4
PWM_I: JP10.1; also elsewhere on the board
REF_H: JP9.3; also elsewhere on the board
REF_L: JP9.1; also elsewhere on the board
REF_R: JP9.5; also elsewhere on the board
RESET: X1.3; also elsewhere on the board
RES_FET: X2.4; also elsewhere on the board
SCK: X1.8; also elsewhere on the board
STEP: JP10.2; also elsewhere on the board
TH_FET: R30.1, R31.2, U18.3 (INA+)
UART_RX: JP6.1; also elsewhere on the board
UART_TX: JP6.2; also elsewhere on the board
V+: R23.2, R25.2, X2.2; also elsewhere on the board
V_EXT: R27.1, R28.2, X1.13
V_GD: JP4.1; also elsewhere on the board
V_INT: R25.1, R26.2, X1.14
V_INT_TMC: U18.8 (OUTC), U18.9 (INC-), U18.12 (IND+); also elsewhere on the board
V_INT_TMC_RAW: R23.1, R24.2, U18.10 (INC+)
V_MOT_IN: R27.2, X2.3; also elsewhere on the board

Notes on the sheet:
Motor
Encoder Terminal
Hall Input
GPIO
MOTOR SUPPLY
Interconnect
UART
SPI Selection
LEDs
Connectors
Testpoints
Analog Encoder
Single ended jumper
1.5k - 1n?
Input 5V -> 3.3V buffer
MCP6004 or MCP6009
Voltage Sense
60V=>1.25V 65V=>1.336
Temperature sense mosfets
Thermistor 10k
Brake resistor forced activation point
Limit should be set to 1.7V max! Linear range up to 1.25V
1.3V
Use 1nF to 4.7nF filter caps

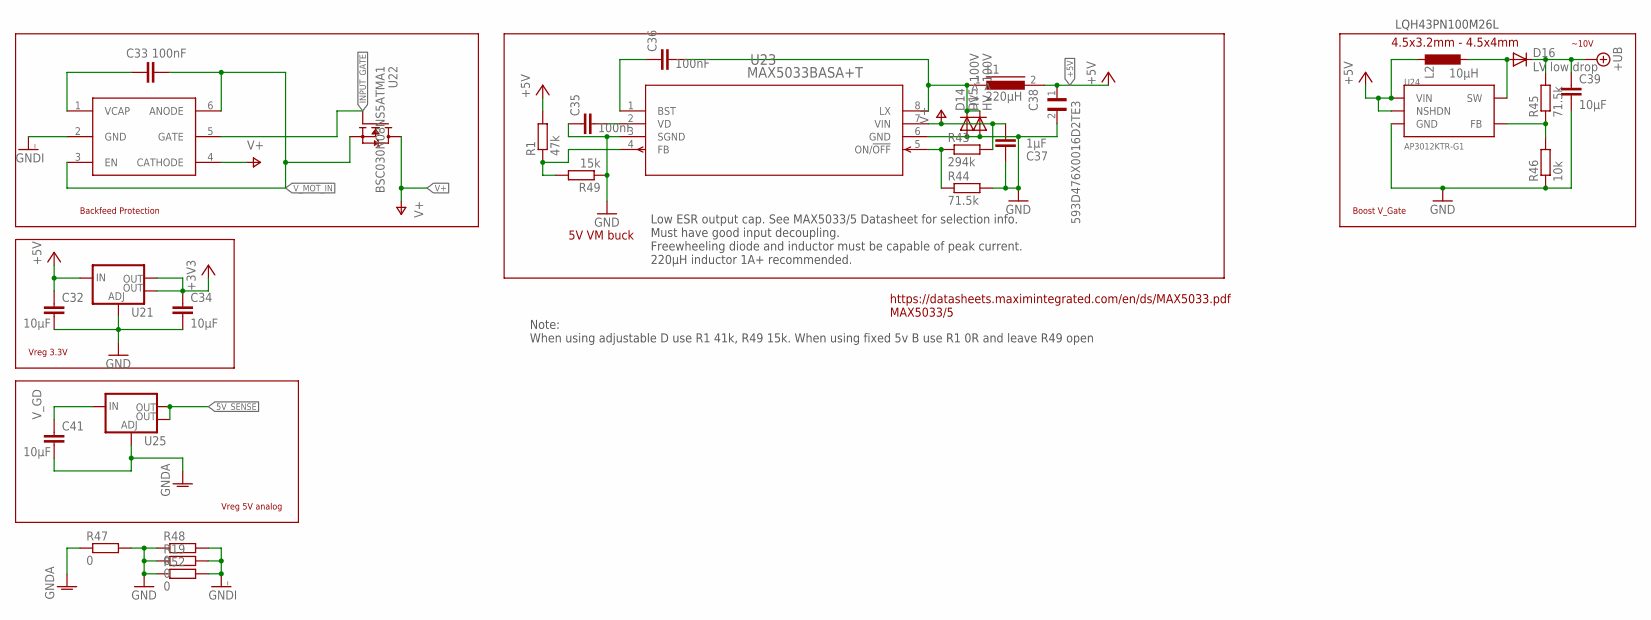
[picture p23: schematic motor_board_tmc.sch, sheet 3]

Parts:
C32, C34, C39, C41: 10µF; C0805
C33, C35, C36: 100nF; C0603
C37: 1µF; C1206
C38: 593D476X0016D2TE3; CAPPM7343X310N
D14: HV >100V; SOD-123FL
D15: HV >100V; SMADIODE
D16: LV low drop; SOD-123FL
L1: 220µH; 8MMINDUCTOR
L2: 10µH; L4532P
R1: 47k; R0603
R19, R47, R48, R52: 0; R0603
R43: 294k; R0805
R44, R45: 71.5k; R0805
R46: 10k; R0603
R49: 15k; R0603
U20: LM74700-Q1; SOT23-6
U21, U25: V_REG_LM1117SOT223; SOT223
U22: BSC030N08NS5ATMA1; MOSFET_BSC093N04LSGATMA1
U23: MAX5033BASA+T; 21-0041B_8_MXM
U24: AP3012KTR-G1; SOT23-5L

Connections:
5V_SENSE: U25.2 (OUT), U25.4 (OUT); also elsewhere on the board
+3V3: C34.1, U21.2 (OUT), U21.4 (OUT); also elsewhere on the board
+5V: C32.1, C38.1, L1.2, L2.1, R1.2, U21.3 (IN), U24.4 (NSHDN), U24.5 (VIN); also elsewhere on the board
GND: C32.2, C34.2, C35.1, C37.1, C38.2, C39.2, D14.A, D15.A, R19.1, R44.2, R46.1, R47.2, R48.1, R49.1, R52.1, U21.1 (ADJ), U23.3 (SGND), U23.6 (GND), U24.2 (GND); also elsewhere on the board
GNDA: C41.2, R47.1, U25.1 (ADJ); also elsewhere on the board
GNDI: R19.2, R48.2, R52.2, U20.2 (GND); also elsewhere on the board
INPUT_GATE: U20.5 (GATE), U22.4 (G)
unnamed: R45.1, R46.2, U24.3 (FB)
unnamed: R1.1, R49.2, U23.4 (FB)
unnamed: D16.A, L2.2, U24.1 (SW)
unnamed: C36.2, D14.C, D15.C, L1.1, U23.8 (LX)
unnamed: C36.1, U23.1 (BST)
unnamed: R43.1, R44.1, U23.5 (ON/!OFF)
unnamed: C33.1, U20.1 (VCAP)
unnamed: C35.2, U23.2 (VD)
V+: C37.2, R43.2, U20.4 (CATHODE), U22.5 (D), U23.7 (VIN); also elsewhere on the board
V_GD: C39.1, C41.1, D16.C, R45.2, U25.3 (IN); also elsewhere on the board
V_MOT_IN: C33.2, U20.3 (EN), U20.6 (ANODE), U22.1 (S), U22.2 (S), U22.3 (S); also elsewhere on the board

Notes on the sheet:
Vreg 3.3V
Backfeed Protection
Boost V_Gate
~10V
4.5x3.2mm - 4.5x4mm
5V VM buck
https://datasheets.maximintegrated.com/en/ds/MAX5033.pdf MAX5033/5
LQH43PN100M26L
Low ESR output cap. See MAX5033/5 Datasheet for selection info. Must have good input decoupling. Freewheeling diode and inductor must be capable of peak current. 220µH inductor 1A+ recommended.
Vreg 5V analog
Note: When using adjustable D use R1 41k, R49 15k. When using fixed 5v B use R1 0R and leave R49 open

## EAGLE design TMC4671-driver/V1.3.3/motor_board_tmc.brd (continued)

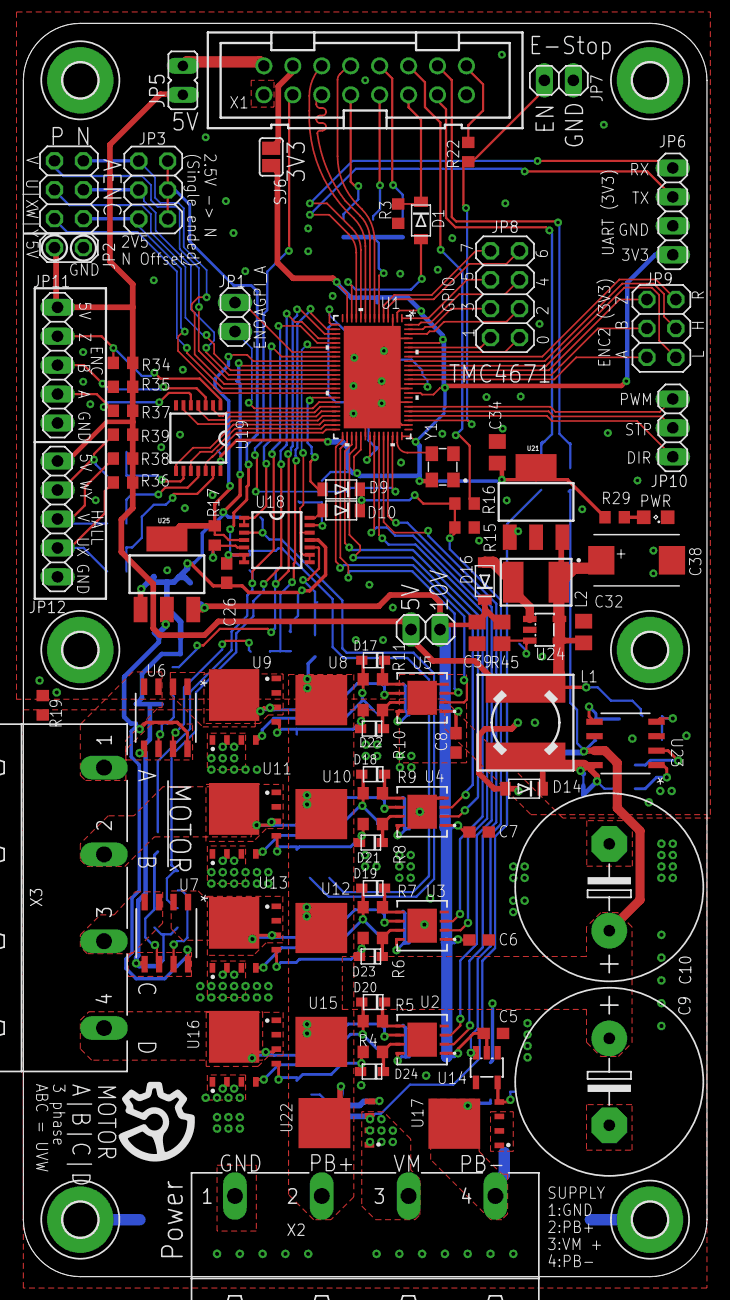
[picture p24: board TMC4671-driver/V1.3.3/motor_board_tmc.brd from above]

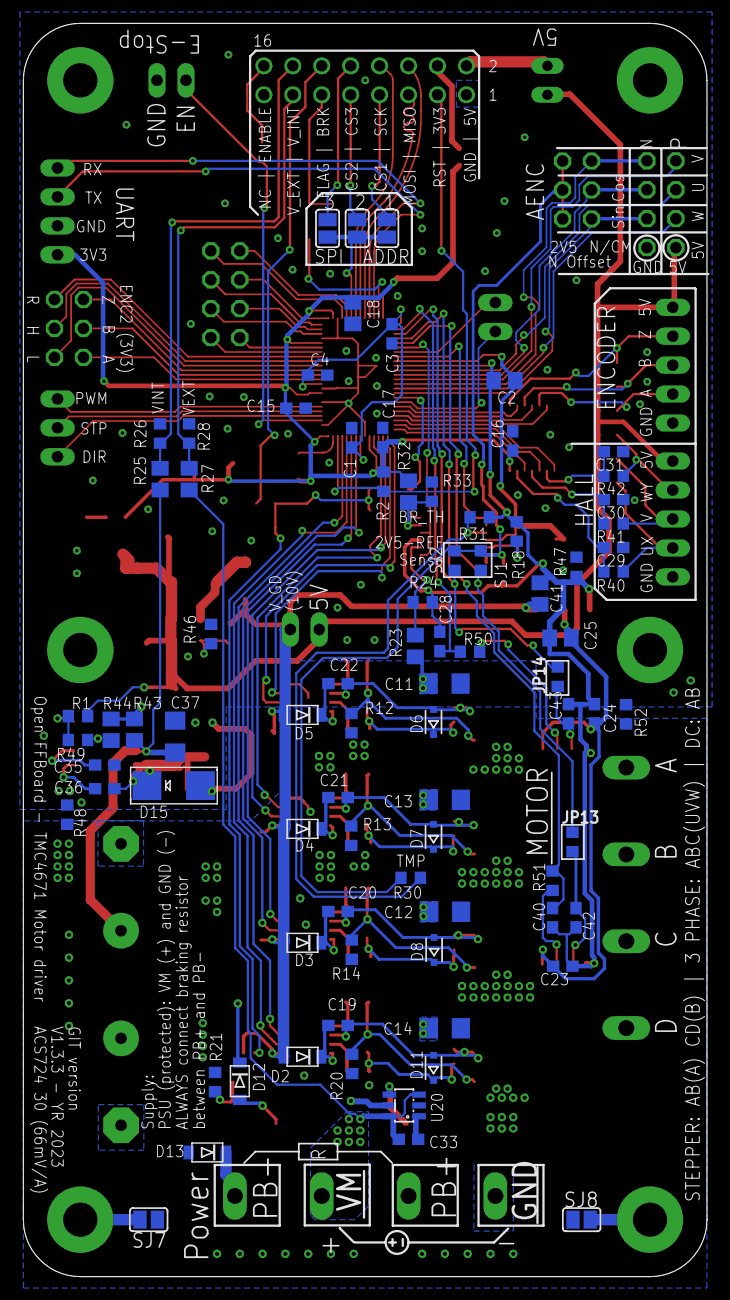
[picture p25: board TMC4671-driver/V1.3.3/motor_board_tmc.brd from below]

Board: 2 copper layers, 60.0 x 110.0 mm, 178 parts (82 on the bottom side), 136 nets.

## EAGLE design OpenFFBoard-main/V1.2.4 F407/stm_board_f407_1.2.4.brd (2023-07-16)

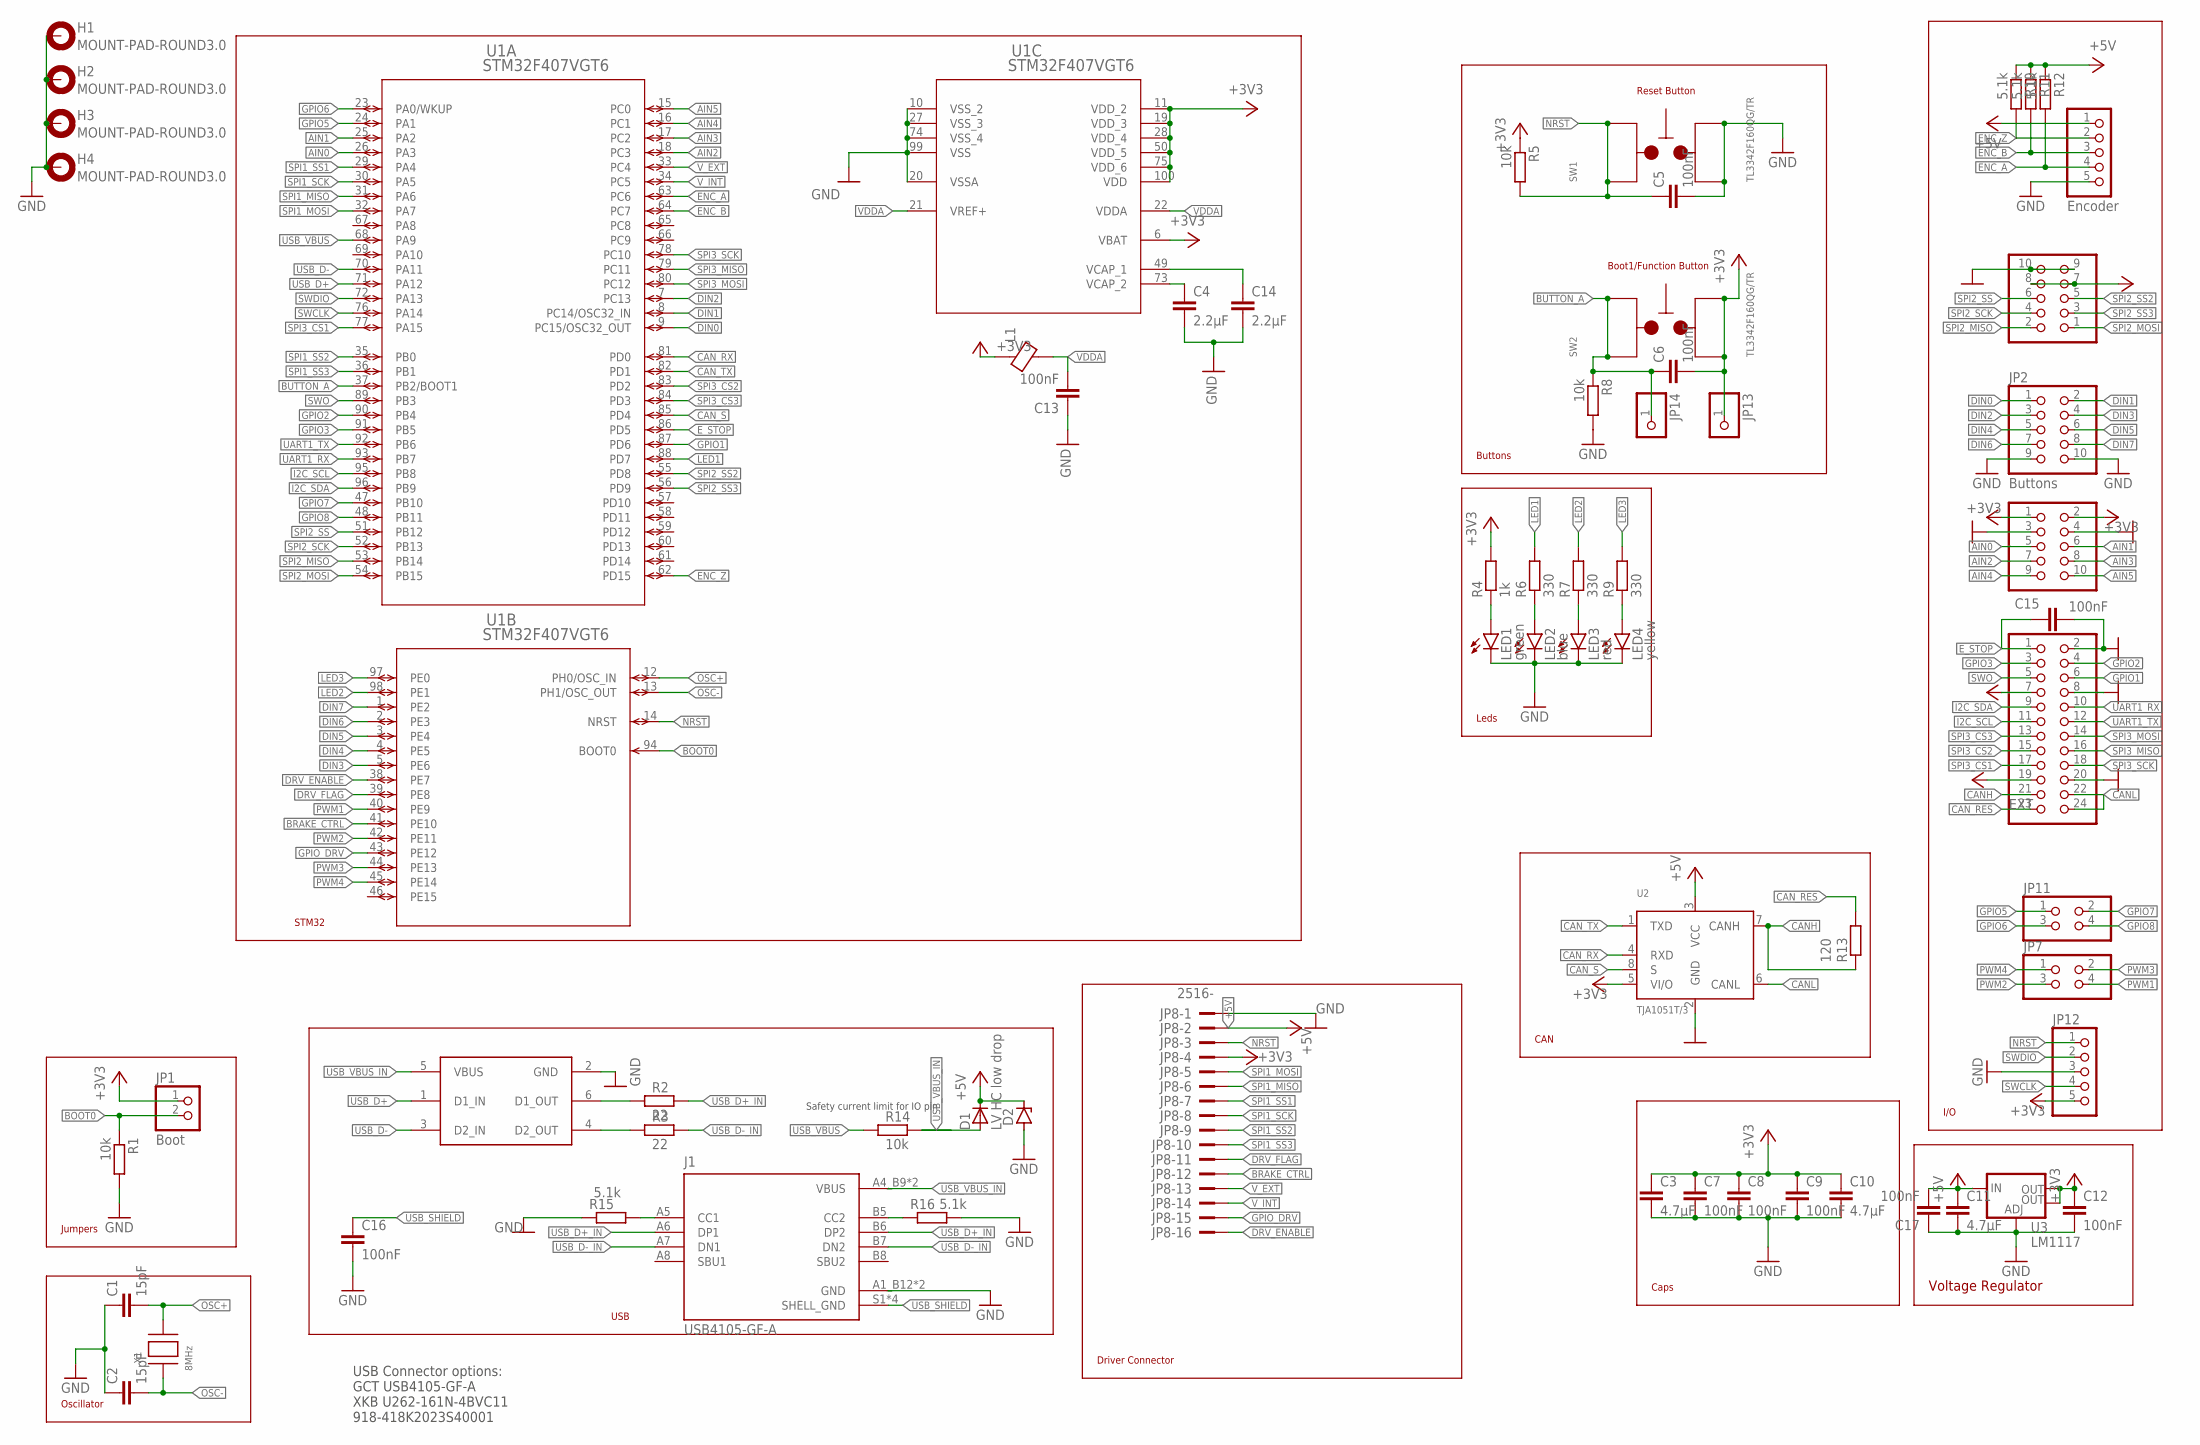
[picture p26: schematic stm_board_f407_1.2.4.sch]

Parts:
C1, C2: 15pF; C0603
C3, C10, C11: 4.7µF; C0805
C4, C14: 2.2µF; C0603
C5, C6, C7, C8, C9, C12, C13, C15, C16, C17: 100nF; C0603
D1: LV HC low drop; SMADIODE
D2: ZENER-DIODESOD80C; SOD80C
H1, H2, H3, H4: MOUNT-PAD-ROUND3.0; 3,0-PAD
J1: USB4105-GF-A; GCT_USB4105-GF-A
JP1: Boot; 1X02
JP2: Buttons; 2X05
JP3: Analog; 2X05
JP4: EXT; 2X12
JP5: Encoder; 1X05
JP6: SPI; 2X05
JP7, JP11: PINHD-2X2; 2X02
JP8: 2516-; PAK100/2500-16
JP12: PINHD-1X5; 1X05
JP13, JP14: PINHD-1X1; 1X01
L1: GZ2012D601TF; BLM21PG331SN1D
LED1: green; SML0805
LED2: blue; SML0805
LED3: red; SML0805
LED4: yellow; SML0805
R1, R5, R8, R14: 10k; R0603
R2, R3: 22; R0603
R4: 1k; R0603
R6, R7, R9: 330; R0603
R10, R11, R12, R15, R16: 5.1k; R0603
R13: 120; R0603
SW1, SW2: TL3342F160QG/TR
U1: STM32F407VGT6; LQFP100-14X14MM
U2: TJA1051T/3; SOT96-1
U3: LM1117; SOT223
U4: USBLC6-2SC6; TSOT-23-6
X1: 8MHz; NX5032

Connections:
+3V3: C3.1, C6.2, C7.1, C8.1, C9.1, C10.1, C12.1, JP1.1, JP3.1, JP3.2, JP4.7, JP6.7, JP6.8, JP8.4, JP12.5, JP13.1, L1.1, R4.2, R5.1, SW2.1, SW2.2, U1.6 (VBAT), U1.11 (VDD_2), U1.19 (VDD_3), U1.28 (VDD_4), U1.50 (VDD_5), U1.75 (VDD_6), U1.100 (VDD), U2.5 (VI/O), U3.2 (OUT), U3.4 (OUT)
+5V: C11.1, C17.2, D1.C, D2.C, JP4.19, JP5.1, JP8.2, R10.1, R11.1, R12.1, U2.3 (VCC), U3.3 (IN)
AIN0: JP3.5, U1.26 (PA3)
AIN1: JP3.6, U1.25 (PA2)
AIN2: JP3.7, U1.18 (PC3)
AIN3: JP3.8, U1.17 (PC2)
AIN4: JP3.9, U1.16 (PC1)
AIN5: JP3.10, U1.15 (PC0)
BOOT0: JP1.2, R1.1, U1.94 (BOOT0)
BRAKE_CTRL: JP8.12, U1.41 (PE10)
BUTTON_A: C6.1, JP14.1, R8.1, SW2.3, SW2.4, U1.37 (PB2/BOOT1)
CANH: JP4.21, R13.1, U2.7 (CANH)
CANL: JP4.22, JP4.24, U2.6 (CANL)
CAN_RES: JP4.23, R13.2
CAN_RX: U1.81 (PD0), U2.4 (RXD)
CAN_S: U1.85 (PD4), U2.8 (S)
CAN_TX: U1.82 (PD1), U2.1 (TXD)
DIN0: JP2.1, U1.9 (PC15/OSC32_OUT)
DIN1: JP2.2, U1.8 (PC14/OSC32_IN)
DIN2: JP2.3, U1.7 (PC13)
DIN3: JP2.4, U1.5 (PE6)
DIN4: JP2.5, U1.4 (PE5)
DIN5: JP2.6, U1.3 (PE4)
DIN6: JP2.7, U1.2 (PE3)
DIN7: JP2.8, U1.1 (PE2)
DRV_ENABLE: JP8.16, U1.38 (PE7)
DRV_FLAG: JP8.11, U1.39 (PE8)
ENC_A: JP5.4, R12.2, U1.63 (PC6)
ENC_B: JP5.3, R11.2, U1.64 (PC7)
ENC_Z: JP5.2, R10.2, U1.62 (PD15)
E_STOP: C15.1, JP4.1, U1.86 (PD5)
GND: C1.1, C2.1, C3.2, C4.2, C5.2, C7.2, C8.2, C9.2, C10.2, C11.2, C12.2, C13.1, C14.2, C15.2, C16.2, C17.1, D2.A, H1.B3,0, H2.B3,0, H3.B3,0, H4.B3,0, J1.A1_B12 (GND), J1.B1_A12 (GND), JP2.9, JP2.10, JP3.3, JP3.4, JP4.2, JP4.8, JP4.20, JP5.5, JP6.9, JP6.10, JP8.1, JP12.3, LED1.C, LED2.C, LED3.C, LED4.C, R1.2, R8.2, R15.1, R16.2, SW1.1, SW1.2, U1.10 (VSS_2), U1.20 (VSSA), U1.27 (VSS_3), U1.74 (VSS_4), U1.99 (VSS), U2.2 (GND), U3.1 (ADJ), U4.2 (GND)
GPIO1: JP4.6, U1.87 (PD6)
GPIO2: JP4.4, U1.90 (PB4)
GPIO3: JP4.3, U1.91 (PB5)
GPIO5: JP11.1, U1.24 (PA1)
GPIO6: JP11.3, U1.23 (PA0/WKUP)
GPIO7: JP11.2, U1.47 (PB10)
GPIO8: JP11.4, U1.48 (PB11)
GPIO_DRV: JP8.15, U1.43 (PE12)
I2C_SCL: JP4.11, U1.95 (PB8)
I2C_SDA: JP4.9, U1.96 (PB9)
LED1: R6.2, U1.88 (PD7)
LED2: R7.2, U1.98 (PE1)
LED3: R9.2, U1.97 (PE0)
unnamed: R2.1, U4.6 (D1_OUT)
unnamed: LED4.A, R9.1
unnamed: C14.1, U1.49 (VCAP_1)
unnamed: J1.B5 (CC2), R16.1
unnamed: J1.A5 (CC1), R15.2
unnamed: C4.1, U1.73 (VCAP_2)
unnamed: R3.1, U4.4 (D2_OUT)
unnamed: LED1.A, R4.1
unnamed: LED2.A, R6.1
unnamed: LED3.A, R7.1
NRST: C5.1, JP8.3, JP12.1, R5.2, SW1.3, SW1.4, U1.14 (NRST)
OSC+: C1.2, U1.12 (PH0/OSC_IN), X1.P$2
OSC-: C2.2, U1.13 (PH1/OSC_OUT), X1.P$1
PWM1: JP7.4, U1.40 (PE9)
PWM2: JP7.3, U1.42 (PE11)
PWM3: JP7.2, U1.44 (PE13)
PWM4: JP7.1, U1.45 (PE14)
SPI1_MISO: JP8.6, U1.31 (PA6)
SPI1_MOSI: JP8.5, U1.32 (PA7)
SPI1_SCK: JP8.8, U1.30 (PA5)
SPI1_SS1: JP8.7, U1.29 (PA4)
SPI1_SS2: JP8.9, U1.35 (PB0)
SPI1_SS3: JP8.10, U1.36 (PB1)
SPI2_MISO: JP6.2, U1.53 (PB14)
SPI2_MOSI: JP6.1, U1.54 (PB15)
SPI2_SCK: JP6.4, U1.52 (PB13)
SPI2_SS: JP6.6, U1.51 (PB12)
SPI2_SS2: JP6.5, U1.55 (PD8)
SPI2_SS3: JP6.3, U1.56 (PD9)
SPI3_CS1: JP4.17, U1.77 (PA15)
SPI3_CS2: JP4.15, U1.83 (PD2)
SPI3_CS3: JP4.13, U1.84 (PD3)
SPI3_MISO: JP4.16, U1.79 (PC11)
SPI3_MOSI: JP4.14, U1.80 (PC12)
SPI3_SCK: JP4.18, U1.78 (PC10)
SWCLK: JP12.4, U1.76 (PA14)
SWDIO: JP12.2, U1.72 (PA13)
SWO: JP4.5, U1.89 (PB3)
UART1_RX: JP4.10, U1.93 (PB7)
UART1_TX: JP4.12, U1.92 (PB6)
USB_D+: U1.71 (PA12), U4.1 (D1_IN)
USB_D+_IN: J1.A6 (DP1), J1.B6 (DP2), R2.2
USB_D-: U1.70 (PA11), U4.3 (D2_IN)
USB_D-_IN: J1.A7 (DN1), J1.B7 (DN2), R3.2
USB_SHIELD: C16.1, J1.S1 (SHELL_GND), J1.S2 (SHELL_GND), J1.S3 (SHELL_GND), J1.S4 (SHELL_GND)
USB_VBUS: R14.1, U1.68 (PA9)
USB_VBUS_IN: D1.A, J1.A4_B9 (VBUS), J1.B4_A9 (VBUS), R14.2, U4.5 (VBUS)
VDDA: C13.2, L1.2, U1.21 (VREF+), U1.22 (VDDA)
V_EXT: JP8.13, U1.33 (PC4)
V_INT: JP8.14, U1.34 (PC5)

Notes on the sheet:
Oscillator
USB
Boot1/Function Button
Reset Button
Buttons
Jumpers
Leds
Voltage Regulator
I/O
Driver Connector
Caps
STM32
Safety current limit for IO pin
CAN
USB Connector options: GCT USB4105-GF-A XKB U262-161N-4BVC11 918-418K2023S40001

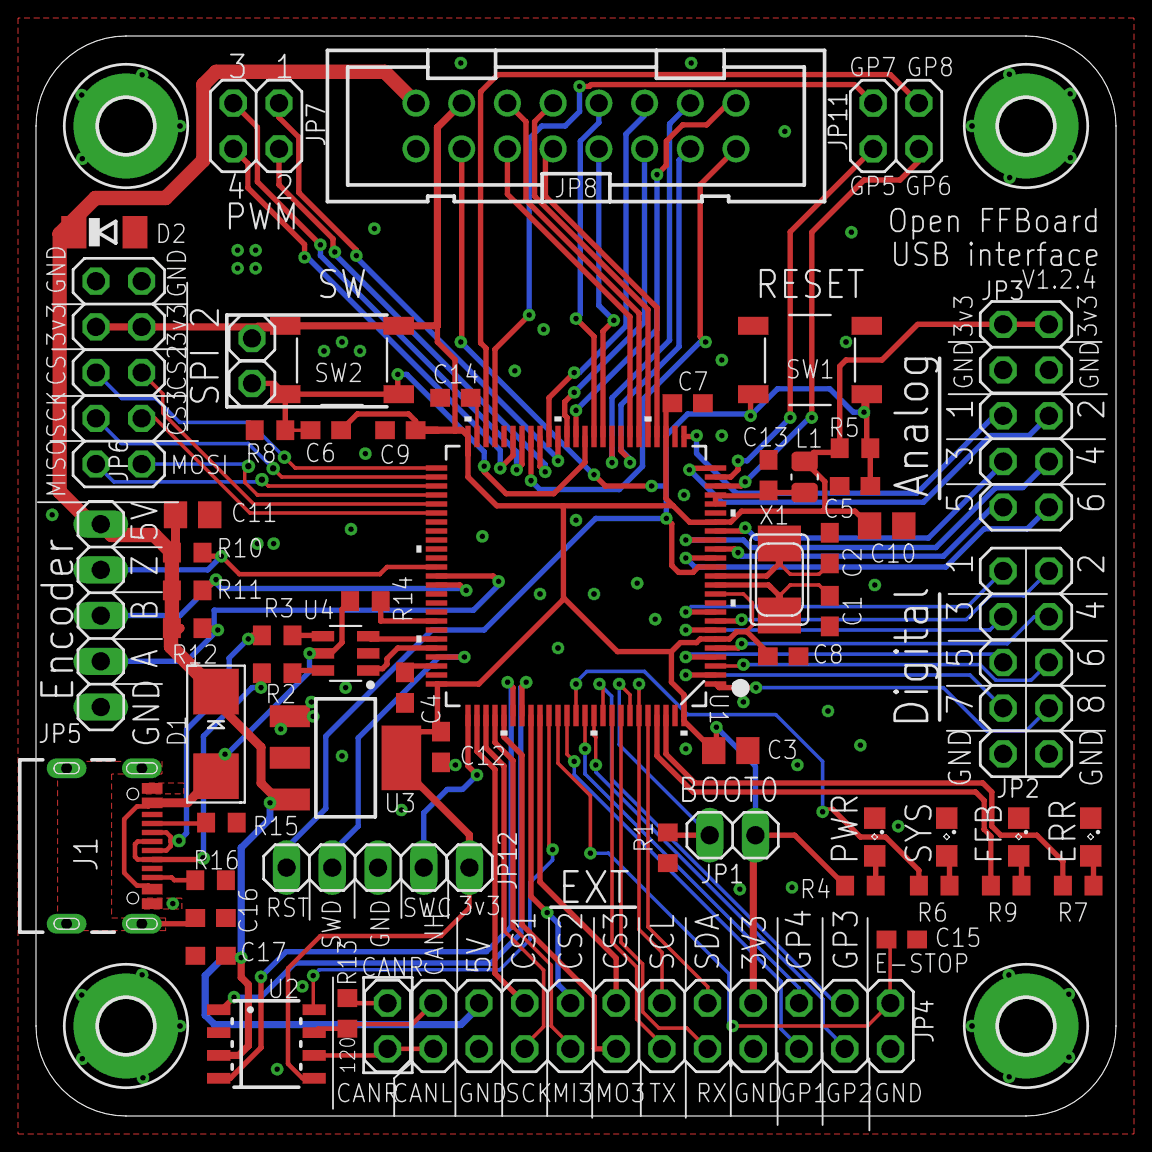
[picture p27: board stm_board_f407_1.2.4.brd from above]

Board: 2 copper layers, 60.0 x 60.0 mm, 64 parts (0 on the bottom side), 95 nets.

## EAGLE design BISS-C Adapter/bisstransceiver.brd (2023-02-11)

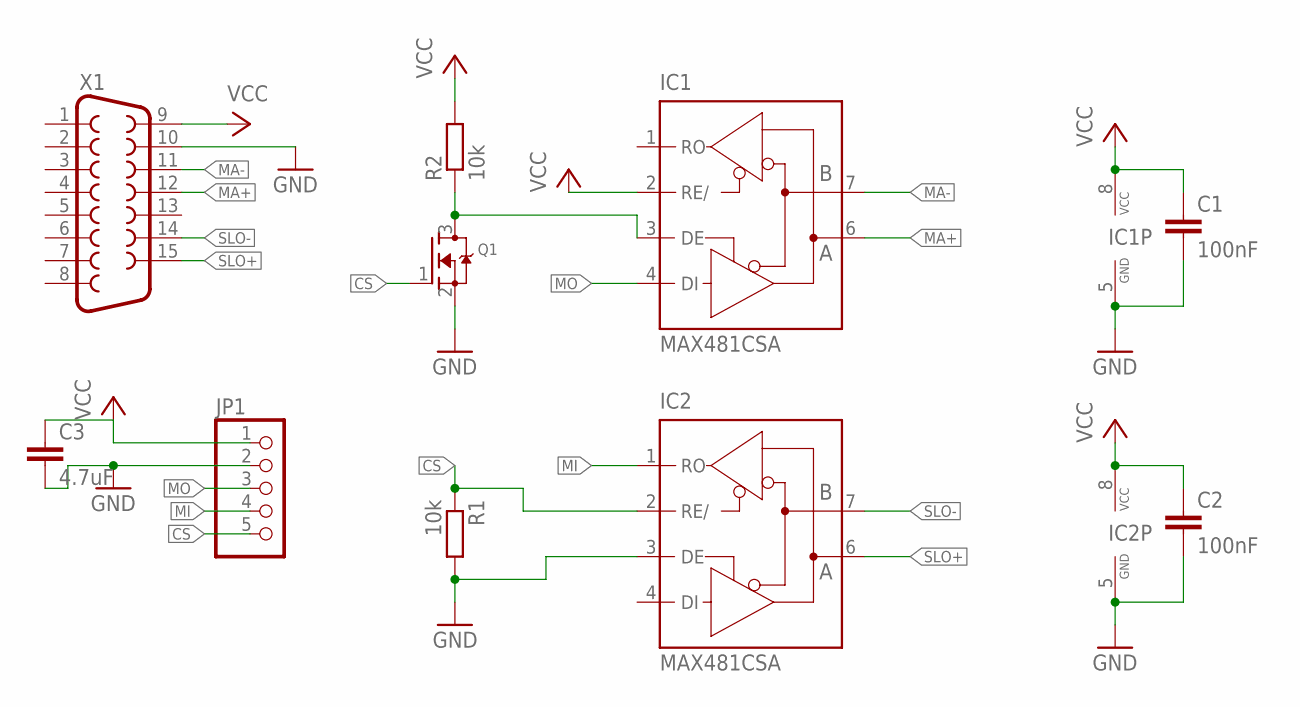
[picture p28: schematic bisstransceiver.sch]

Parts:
C1, C2: 100nF; C0603
C3: 4.7uF; C0603
IC1, IC2: MAX481CSA; SO08
JP1: PINHD-1X5/90; 1X05/90
Q1: MOSFET-NREFLOW; SOT23
R1, R2: 10k; R0603
X1: F15HP

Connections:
CS: IC2.2 (RE/), JP1.5, Q1.1 (G), R1.1
GND: C1.2, C2.2, C3.2, IC1.5 (GND), IC2.3 (DE), IC2.5 (GND), JP1.2, Q1.2 (S), R1.2, X1.10
MA+: IC1.6 (A), X1.12
MA-: IC1.7 (B), X1.11
MI: IC2.1 (RO), JP1.4
MO: IC1.4 (DI), JP1.3
unnamed: IC1.3 (DE), Q1.3 (D), R2.1
SLO+: IC2.6 (A), X1.15
SLO-: IC2.7 (B), X1.14
VCC: C1.1, C2.1, C3.1, IC1.2 (RE/), IC1.8 (VCC), IC2.8 (VCC), JP1.1, R2.2, X1.9

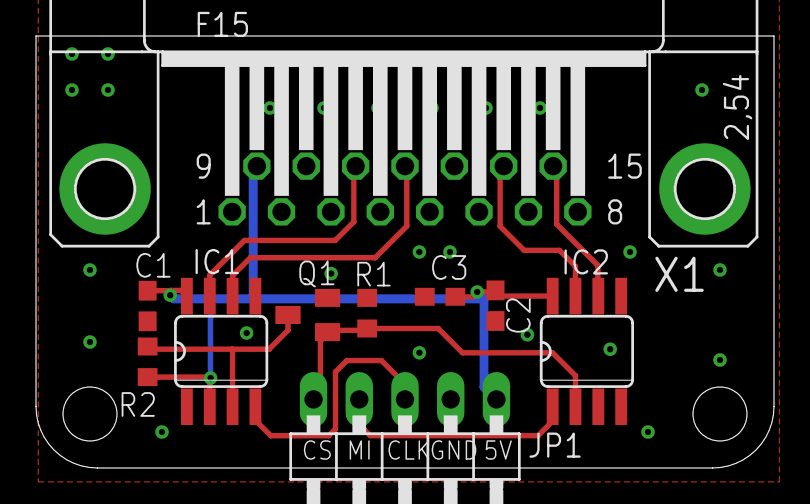
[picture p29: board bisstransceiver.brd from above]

Board: 2 copper layers, 41.0 x 24.0 mm, 10 parts (0 on the bottom side), 10 nets.

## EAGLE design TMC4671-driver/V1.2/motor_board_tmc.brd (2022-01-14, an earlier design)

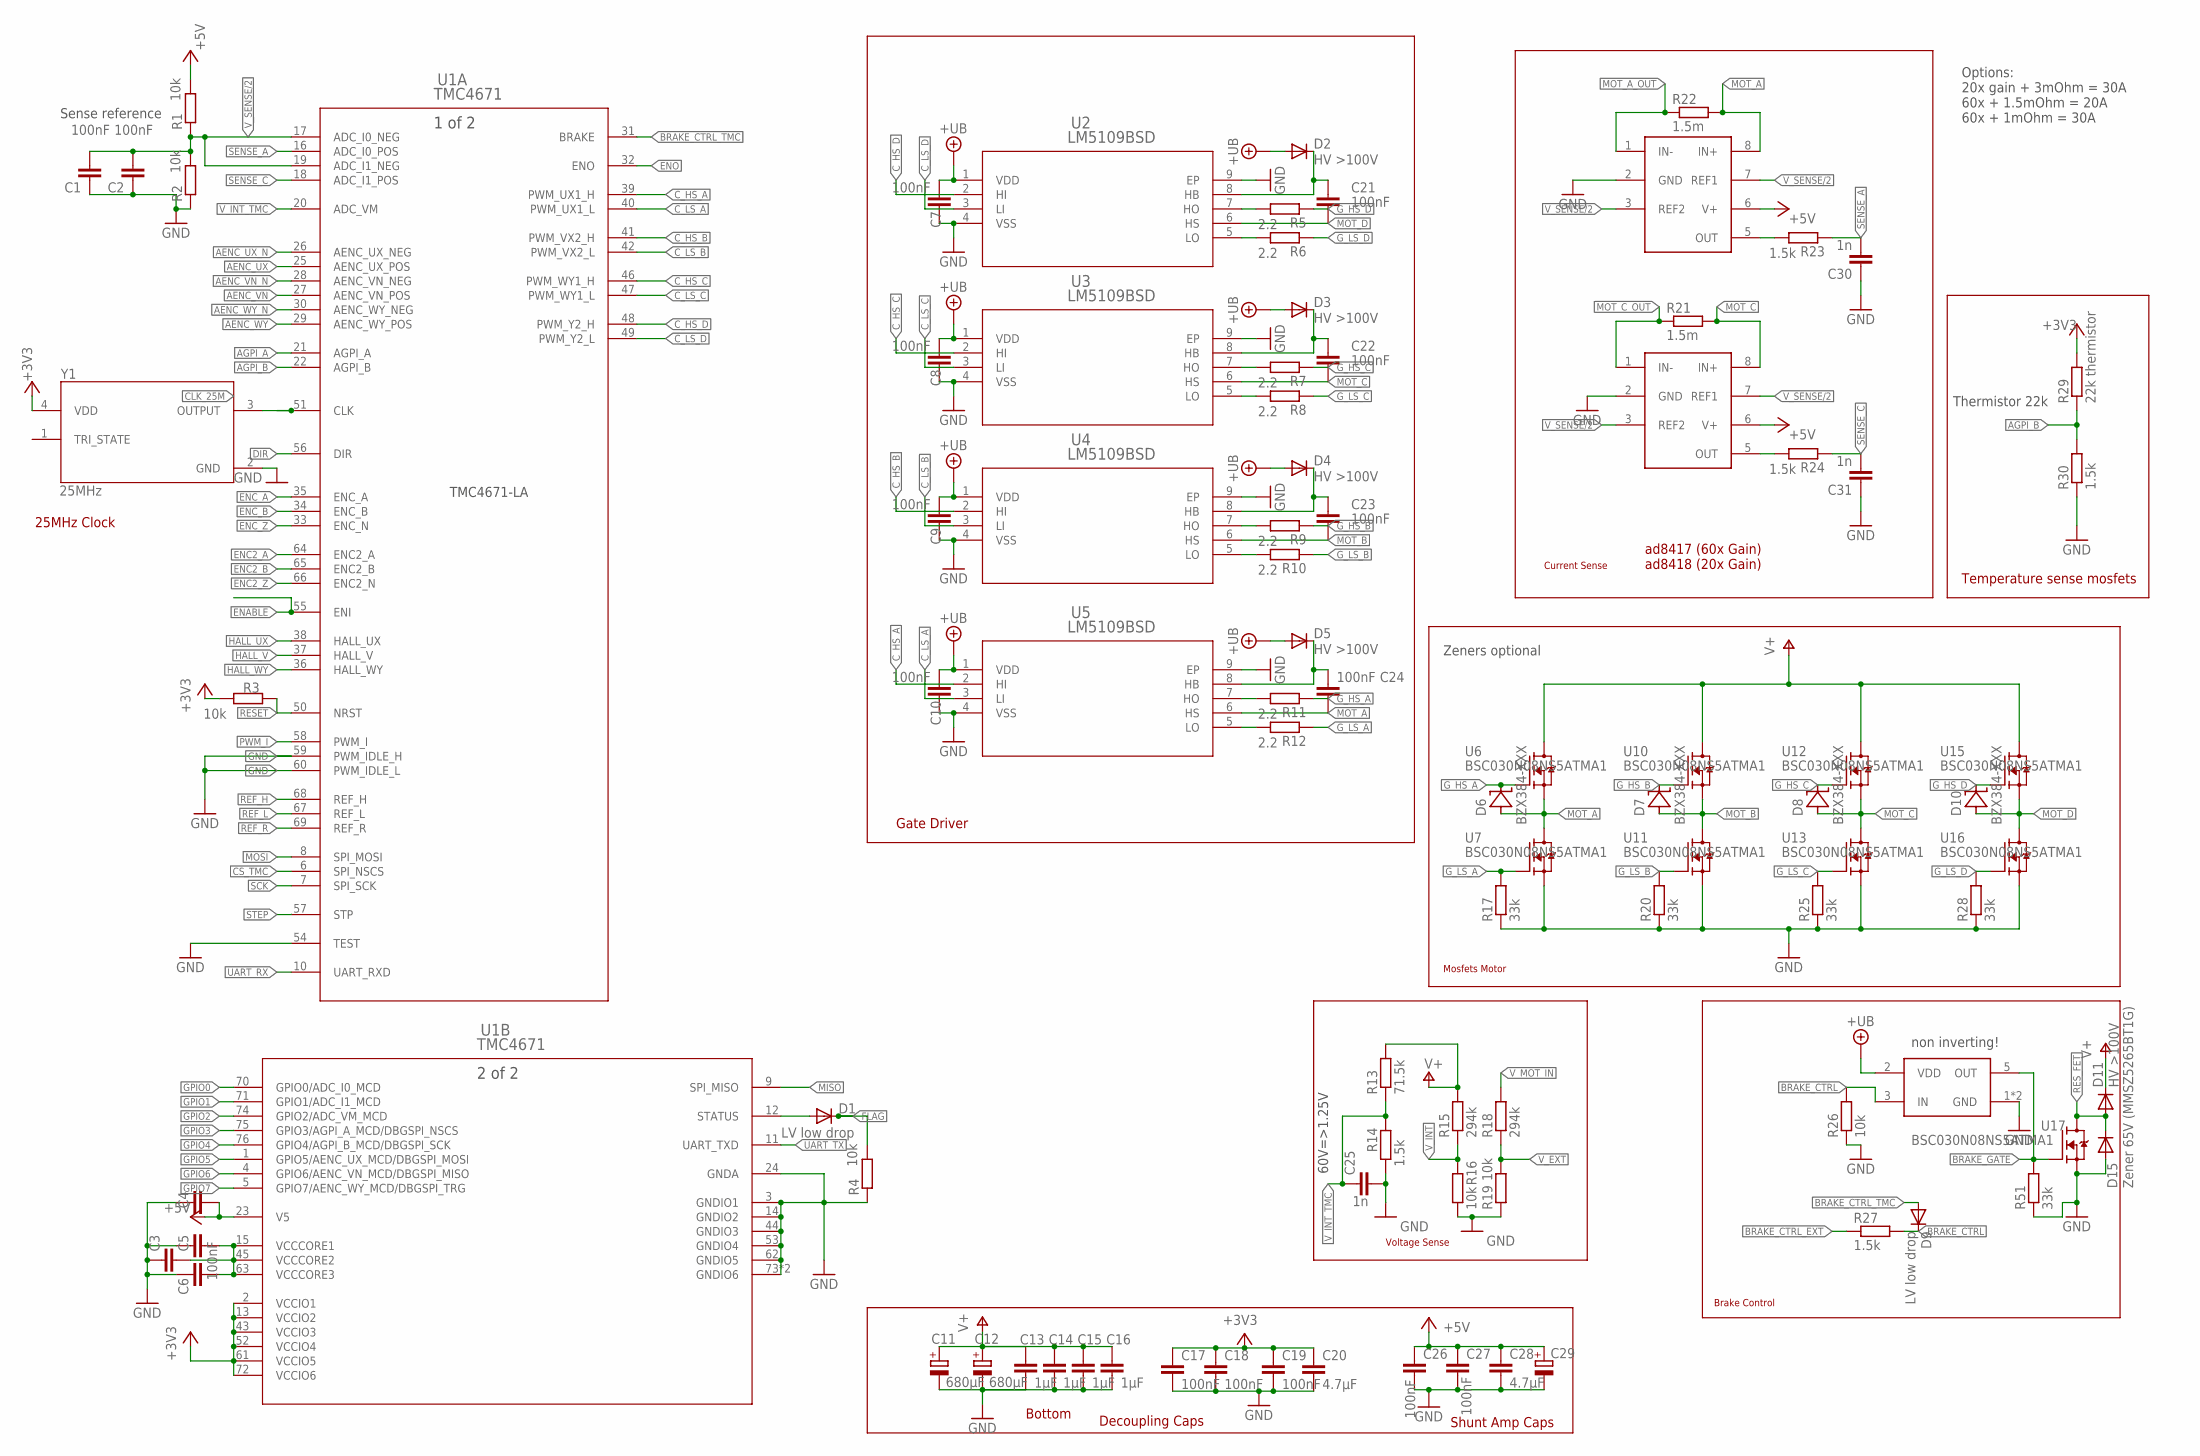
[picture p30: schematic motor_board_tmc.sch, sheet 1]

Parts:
C1, C2, C3, C4, C5, C6, C7, C8, C9, C10, C17, C18, C19, C26, C27: 100nF; C0603
C11, C12: 680µF; E7,5-16
C13, C14, C15, C16: 1µF; C1206
C20, C28: 4.7µF; C0805
C21, C22, C23, C24: 100nF; C0805
C25, C30, C31: 1n; C0603
C29: CPOL-EUE5-8.5; E5-8,5
D1, D9: LV low drop; SOD-123FL
D2, D3, D4, D5, D11: HV >100V; SOD-123FL
D6, D7, D8, D10: BZX384-XXX; SOD323-R
D15: Zener 65V (MMSZ5265BT1G); SOD-123FL
R1, R2, R3, R4, R16, R19, R26: 10k; R0603
R5, R6, R7, R8, R9, R10, R11, R12: 2.2; R0603
R13: 71.5k; R0805
R14, R23, R24, R27, R30: 1.5k; R0603
R15, R18: 294k; R0805
R17, R20, R25, R28, R51: 33k; R0603
R21, R22: 1.5m; R2512
R29: 22k thermistor; R0603
U1: TMC4671; QFN76_10P5X6P5
U2, U3, U4, U5: LM5109BSD; SDC08A
U6, U7, U10, U11, U12, U13, U15, U16, U17: BSC030N08NS5ATMA1; MOSFET_BSC093N04LSGATMA1
U8, U9: AD841X; MSOP8
U14: MCP14XX; SOT23-5L
Y1: 25MHz; ECS-327KE-TR

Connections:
+3V3: C17.1, C18.1, C19.1, C20.1, R3.2, R29.2, U1.2 (VCCIO1), U1.13 (VCCIO2), U1.43 (VCCIO3), U1.52 (VCCIO4), U1.61 (VCCIO5), U1.72 (VCCIO6), Y1.4 (VDD); also elsewhere on the board
+5V: C4.2, C26.1, C27.1, C28.1, C29.+, R1.2, U1.23 (V5), U8.6 (V+), U9.6 (V+); also elsewhere on the board
AENC_UX: U1.25 (AENC_UX_POS); also elsewhere on the board
AENC_UX_N: U1.26 (AENC_UX_NEG); also elsewhere on the board
AENC_VN: U1.27 (AENC_VN_POS); also elsewhere on the board
AENC_VN_N: U1.28 (AENC_VN_NEG); also elsewhere on the board
AENC_WY: U1.29 (AENC_WY_POS); also elsewhere on the board
AENC_WY_N: U1.30 (AENC_WY_NEG); also elsewhere on the board
AGPI_A: U1.21 (AGPI_A); also elsewhere on the board
AGPI_B: R29.1, R30.2, U1.22 (AGPI_B)
BRAKE_CTRL: D9.C, R26.2, R27.2, U14.3 (IN)
BRAKE_CTRL_EXT: R27.1; also elsewhere on the board
BRAKE_CTRL_TMC: D9.A, U1.31 (BRAKE)
BRAKE_GATE: R51.2, U14.5 (OUT), U17.4 (G)
CLK_25M: U1.51 (CLK), Y1.3 (OUTPUT)
CS_TMC: U1.6 (SPI_NSCS); also elsewhere on the board
C_HS_A: U1.39 (PWM_UX1_H), U5.2 (HI)
C_HS_B: U1.41 (PWM_VX2_H), U4.2 (HI)
C_HS_C: U1.46 (PWM_WY1_H), U3.2 (HI)
C_HS_D: U1.48 (PWM_Y2_H), U2.2 (HI)
C_LS_A: U1.40 (PWM_UX1_L), U5.3 (LI)
C_LS_B: U1.42 (PWM_VX2_L), U4.3 (LI)
C_LS_C: U1.47 (PWM_WY1_L), U3.3 (LI)
C_LS_D: U1.49 (PWM_Y2_L), U2.3 (LI)
DIR: U1.56 (DIR); also elsewhere on the board
ENABLE: U1.55 (ENI); also elsewhere on the board
ENC2_A: U1.64 (ENC2_A); also elsewhere on the board
ENC2_B: U1.65 (ENC2_B); also elsewhere on the board
ENC2_Z: U1.66 (ENC2_N); also elsewhere on the board
ENC_A: U1.35 (ENC_A); also elsewhere on the board
ENC_B: U1.34 (ENC_B); also elsewhere on the board
ENC_Z: U1.33 (ENC_N); also elsewhere on the board
ENO: U1.32 (ENO); also elsewhere on the board
FLAG: D1.C, R4.2; also elsewhere on the board
GND: C1.1, C2.1, C3.1, C4.1, C5.1, C6.1, C7.1, C8.1, C9.1, C10.1, C11.-, C12.-, C13.2, C14.2, C15.2, C16.2, C17.2, C18.2, C19.2, C20.2, C25.2, C26.2, C27.2, C28.2, C29.-, C30.1, C31.1, D15.A, R2.1, R4.1, R14.1, R16.1, R17.1, R19.1, R20.1, R25.1, R26.1, R28.1, R30.1, R51.1, U1.3 (GNDIO1), U1.14 (GNDIO2), U1.24 (GNDA), U1.44 (GNDIO3), U1.53 (GNDIO4), U1.54 (TEST), U1.59 (PWM_IDLE_H), U1.60 (PWM_IDLE_L), U1.62 (GNDIO5), U1.73 (GNDIO6), U1.77 (GNDIO6), U2.4 (VSS), U2.9 (EP), U3.4 (VSS), U3.9 (EP), U4.4 (VSS), U4.9 (EP), U5.4 (VSS), U5.9 (EP), U7.1 (S), U7.2 (S), U7.3 (S), U8.2 (GND), U9.2 (GND), U11.1 (S), U11.2 (S), U11.3 (S), U13.1 (S), U13.2 (S), U13.3 (S), U14.1 (GND), U14.4 (GND), U16.1 (S), U16.2 (S), U16.3 (S), U17.1 (S), U17.2 (S), U17.3 (S), Y1.2 (GND); also elsewhere on the board
GPIO0: U1.70 (GPIO0/ADC_I0_MCD); also elsewhere on the board
GPIO1: U1.71 (GPIO1/ADC_I1_MCD); also elsewhere on the board
GPIO2: U1.74 (GPIO2/ADC_VM_MCD); also elsewhere on the board
GPIO3: U1.75 (GPIO3/AGPI_A_MCD/DBGSPI_NSCS); also elsewhere on the board
GPIO4: U1.76 (GPIO4/AGPI_B_MCD/DBGSPI_SCK); also elsewhere on the board
GPIO5: U1.1 (GPIO5/AENC_UX_MCD/DBGSPI_MOSI); also elsewhere on the board
GPIO6: U1.4 (GPIO6/AENC_VN_MCD/DBGSPI_MISO); also elsewhere on the board
GPIO7: U1.5 (GPIO7/AENC_WY_MCD/DBGSPI_TRG); also elsewhere on the board
G_HS_A: D6.C, R11.1, U6.4 (G)
G_HS_B: D7.C, R9.1, U10.4 (G)
G_HS_C: D8.C, R7.1, U12.4 (G)
G_HS_D: D10.C, R5.1, U15.4 (G)
G_LS_A: R12.1, R17.2, U7.4 (G)
G_LS_B: R10.1, R20.2, U11.4 (G)
G_LS_C: R8.1, R25.2, U13.4 (G)
G_LS_D: R6.1, R28.2, U16.4 (G)
HALL_UX: U1.38 (HALL_UX); also elsewhere on the board
HALL_V: U1.37 (HALL_V); also elsewhere on the board
HALL_WY: U1.36 (HALL_WY); also elsewhere on the board
MISO: U1.9 (SPI_MISO); also elsewhere on the board
MOSI: U1.8 (SPI_MOSI); also elsewhere on the board
MOT_A: C24.2, D6.A, R22.2, U5.6 (HS), U6.1 (S), U6.2 (S), U6.3 (S), U7.5 (D), U8.8 (IN+)
MOT_A_OUT: R22.1, U8.1 (IN-); also elsewhere on the board
MOT_B: C23.2, D7.A, U4.6 (HS), U10.1 (S), U10.2 (S), U10.3 (S), U11.5 (D); also elsewhere on the board
MOT_C: C22.2, D8.A, R21.2, U3.6 (HS), U9.8 (IN+), U12.1 (S), U12.2 (S), U12.3 (S), U13.5 (D)
MOT_C_OUT: R21.1, U9.1 (IN-); also elsewhere on the board
MOT_D: C21.2, D10.A, U2.6 (HS), U15.1 (S), U15.2 (S), U15.3 (S), U16.5 (D); also elsewhere on the board
unnamed: D1.A, U1.12 (STATUS)
unnamed: R23.2, U8.5 (OUT)
unnamed: R24.2, U9.5 (OUT)
unnamed: R12.2, U5.5 (LO)
unnamed: C24.1, D5.C, U5.8 (HB)
unnamed: R11.2, U5.7 (HO)
unnamed: C23.1, D4.C, U4.8 (HB)
unnamed: R10.2, U4.5 (LO)
unnamed: R9.2, U4.7 (HO)
unnamed: C21.1, D2.C, U2.8 (HB)
unnamed: R6.2, U2.5 (LO)
unnamed: R5.2, U2.7 (HO)
unnamed: C22.1, D3.C, U3.8 (HB)
unnamed: R8.2, U3.5 (LO)
unnamed: R7.2, U3.7 (HO)
PWM_I: U1.58 (PWM_I); also elsewhere on the board
REF_H: U1.68 (REF_H); also elsewhere on the board
REF_L: U1.67 (REF_L); also elsewhere on the board
REF_R: U1.69 (REF_R); also elsewhere on the board
RESET: R3.1, U1.50 (NRST); also elsewhere on the board
RES_FET: D11.A, D15.C, U17.5 (D); also elsewhere on the board
SCK: U1.7 (SPI_SCK); also elsewhere on the board
SENSE_A: C30.2, R23.1, U1.16 (ADC_I0_POS)
SENSE_C: C31.2, R24.1, U1.18 (ADC_I1_POS)
STEP: U1.57 (STP); also elsewhere on the board
UART_RX: U1.10 (UART_RXD); also elsewhere on the board
UART_TX: U1.11 (UART_TXD); also elsewhere on the board
V+: C11.+, C12.+, C13.1, C14.1, C15.1, C16.1, D11.C, R13.2, R15.2, U6.5 (D), U10.5 (D), U12.5 (D), U15.5 (D); also elsewhere on the board
VCORE: C3.2, C5.2, C6.2, U1.15 (VCCCORE1), U1.45 (VCCCORE2), U1.63 (VCCCORE3)
V_EXT: R18.1, R19.2; also elsewhere on the board
V_GD: C7.2, C8.2, C9.2, C10.2, D2.A, D3.A, D4.A, D5.A, U2.1 (VDD), U3.1 (VDD), U4.1 (VDD), U5.1 (VDD), U14.2 (VDD); also elsewhere on the board
V_INT: R15.1, R16.2; also elsewhere on the board
V_INT_TMC: C25.1, R13.1, R14.2, U1.20 (ADC_VM)
V_MOT_IN: R18.2; also elsewhere on the board
V_SENSE/2: C1.2, C2.2, R1.1, R2.2, U1.17 (ADC_I0_NEG), U1.19 (ADC_I1_NEG), U8.3 (REF2), U8.7 (REF1), U9.3 (REF2), U9.7 (REF1)

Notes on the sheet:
Mosfets Motor
Gate Driver
Current Sense
Voltage Sense
Brake Control
ad8417 (60x Gain) ad8418 (20x Gain)
Shunt Amp Caps
Decoupling Caps
25MHz Clock
Bottom
Sense reference
60V=>1.25V
Options: 20x gain + 3mOhm = 30A 60x + 1.5mOhm = 20A 60x + 1mOhm = 30A
Temperature sense mosfets
Thermistor 22k
Zeners optional
TMC4671-LA
non inverting!

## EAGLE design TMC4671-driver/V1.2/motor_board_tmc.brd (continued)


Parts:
C32, C34, C36: 100p; C0603
C33, C35, C37: 1n; C0603
H1, H2, H3, H4, H5, H6: MOUNT-PAD-ROUND3.0; 3,0-PAD
JP1, JP7: PINHD-1X2; 1X02
JP2, JP8: PINHD-2X4; 2X04
JP3, JP9: PINHD-2X3; 2X03
JP4: V_DRV; 1X02
JP5: 5V; JP1
JP6: PINHD-1X4; 1X04
JP10: PINHD-1X3; 1X03
JP11, JP12: PINHD-1X5; 1X05
LED1: Green; SML0805
R31, R41, R42, R43, R44, R45, R46: 1.5k; R0603
R32, R33: 10k; R0603
R34: 330; R0603
R35, R36, R37, R38, R39, R40: 4.7k; R0603
SJ1, SJ2, SJ3: SJ
SJ4: 3.3V; SJ
U18, U19: NC7NZ17K8X-3-BUFFER; VFSOP-8
X1: 2516-; PAK100/2500-16
X2, X3: GMSTBA4

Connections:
+3V3: JP6.4, R34.2, SJ4.2, U18.P$8 (VCC), U19.P$8 (VCC); also elsewhere on the board
+5V: JP2.2, JP4.2, JP5.2, JP11.1, JP12.1, R32.2, R35.2, R36.2, R37.2, R38.2, R39.2, R40.2; also elsewhere on the board
AENC_UX: JP2.6; also elsewhere on the board
AENC_UX_N: JP2.5, JP3.3; also elsewhere on the board
AENC_VN: JP2.8; also elsewhere on the board
AENC_VN_N: JP2.7, JP3.1; also elsewhere on the board
AENC_WY: JP2.4; also elsewhere on the board
AENC_WY_N: JP2.3, JP3.5; also elsewhere on the board
AGPI_A: JP1.2; also elsewhere on the board
BRAKE_CTRL_EXT: X1.12; also elsewhere on the board
CS1: SJ1.1, X1.7
CS2: SJ2.1, X1.9
CS3: SJ3.1, X1.10
CS_TMC: SJ1.2, SJ2.2, SJ3.2; also elsewhere on the board
DIR: JP10.3; also elsewhere on the board
ENABLE: JP7.2, R31.1; also elsewhere on the board
ENC2_A: JP9.2; also elsewhere on the board
ENC2_B: JP9.4; also elsewhere on the board
ENC2_Z: JP9.6; also elsewhere on the board
ENC_A: U18.P$2 (3Y); also elsewhere on the board
ENC_A_5V: C36.2, R46.1, U18.P$6 (3A)
ENC_B: U18.P$5 (2Y); also elsewhere on the board
ENC_B_5V: C34.2, R45.1, U18.P$3 (2A)
ENC_Z: U18.P$7 (1Y); also elsewhere on the board
ENC_Z_5V: C32.2, R44.1, U18.P$1 (1A)
ENO: JP1.1; also elsewhere on the board
FLAG: X1.11; also elsewhere on the board
GND: C32.1, C33.1, C34.1, C35.1, C36.1, C37.1, H1.B3,0, H2.B3,0, H3.B3,0, H4.B3,0, H5.B3,0, H6.B3,0, JP2.1, JP6.3, JP7.1, JP11.5, JP12.5, LED1.C, R33.1, U18.P$4 (GND), U19.P$4 (GND), X1.1, X2.1; also elsewhere on the board
GPIO0: JP8.1; also elsewhere on the board
GPIO1: JP8.2; also elsewhere on the board
GPIO2: JP8.3; also elsewhere on the board
GPIO3: JP8.4; also elsewhere on the board
GPIO4: JP8.5; also elsewhere on the board
GPIO5: JP8.6; also elsewhere on the board
GPIO6: JP8.7; also elsewhere on the board
GPIO7: JP8.8; also elsewhere on the board
HALL_UX: U19.P$2 (3Y); also elsewhere on the board
HALL_UX_5V: C33.2, R41.1, U19.P$6 (3A)
HALL_V: U19.P$5 (2Y); also elsewhere on the board
HALL_V_5V: C35.2, R42.1, U19.P$3 (2A)
HALL_WY: U19.P$7 (1Y); also elsewhere on the board
HALL_WY_5V: C37.2, R43.1, U19.P$1 (1A)
MISO: X1.6; also elsewhere on the board
MOSI: X1.5; also elsewhere on the board
MOT_A_OUT: X3.1; also elsewhere on the board
MOT_B: X3.2; also elsewhere on the board
MOT_C_OUT: X3.3; also elsewhere on the board
MOT_D: X3.4; also elsewhere on the board
unnamed: JP12.4, R37.1, R41.2
unnamed: JP12.3, R39.1, R42.2
unnamed: JP11.4, R38.1, R46.2
unnamed: LED1.A, R34.1
unnamed: JP11.3, R36.1, R45.2
unnamed: JP11.2, R35.1, R44.2
unnamed: JP12.2, R40.1, R43.2
unnamed: R31.2, X1.16
unnamed: SJ4.1, X1.4
unnamed: JP3.2, JP3.4, JP3.6, R32.1, R33.2
unnamed: JP5.1, X1.2
PWM_I: JP10.1; also elsewhere on the board
REF_H: JP9.3; also elsewhere on the board
REF_L: JP9.1; also elsewhere on the board
REF_R: JP9.5; also elsewhere on the board
RESET: X1.3; also elsewhere on the board
RES_FET: X2.4; also elsewhere on the board
SCK: X1.8; also elsewhere on the board
STEP: JP10.2; also elsewhere on the board
UART_RX: JP6.1; also elsewhere on the board
UART_TX: JP6.2; also elsewhere on the board
V+: X2.2; also elsewhere on the board
V_EXT: X1.13; also elsewhere on the board
V_GD: JP4.1; also elsewhere on the board
V_INT: X1.14; also elsewhere on the board
V_MOT_IN: X2.3; also elsewhere on the board

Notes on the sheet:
Motor
Encoder Terminal
Hall Input
GPIO
MOTOR SUPPLY
Interconnect
UART
SPI Selection
LEDs
Connectors
Testpoints
Analog Encoder
Single ended jumper
1.5k - 1n?
Optional filters


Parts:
C38, C40: 4.7µF; C0805
C39: 100nF; C0805
C41, C42: 100nF; C0603
C43: 1µF; C1206
C44: 593D476X0016D2TE3; CAPPM7343X310N
C45: 4.7µF <REMOVE>; C0805
D12: HV >100V; SOD-123FL
D13: 5.6V zener; SOD-123FL
D14: LV low drop; SOD-123FL
L1: 220µH; 8MMINDUCTOR
L2: 10µH; L4532P
R47: 294k; R0805
R48, R49: 71.5k; R0805
R50: 10k; R0603
U20: LM74700-Q1; SOT23-6
U21: V_REG_LM1117SOT223; SOT223
U22: BSC030N08NS5ATMA1; MOSFET_BSC093N04LSGATMA1
U23: MAX5033BASA+T; 21-0041B_8_MXM
U24: AP3012KTR-G1; SOT23-5L

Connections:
+3V3: C40.1, U21.2 (OUT), U21.4 (OUT); also elsewhere on the board
+5V: C38.1, C44.1, D13.C, L1.2, L2.1, U21.3 (IN), U23.4 (FB), U24.4 (NSHDN), U24.5 (VIN); also elsewhere on the board
GND: C38.2, C40.2, C41.1, C43.1, C44.2, C45.2, D12.A, D13.A, R48.2, R50.1, U20.2 (GND), U21.1 (ADJ), U23.3 (SGND), U23.6 (GND), U24.2 (GND); also elsewhere on the board
INPUT_GATE: U20.5 (GATE), U22.4 (G)
unnamed: R49.1, R50.2, U24.3 (FB)
unnamed: D14.A, L2.2, U24.1 (SW)
unnamed: C42.2, D12.C, L1.1, U23.8 (LX)
unnamed: C42.1, U23.1 (BST)
unnamed: R47.1, R48.1, U23.5 (ON/!OFF)
unnamed: C39.1, U20.1 (VCAP)
unnamed: C41.2, U23.2 (VD)
V+: C43.2, R47.2, U20.4 (CATHODE), U22.5 (D), U23.7 (VIN); also elsewhere on the board
V_GD: C45.1, D14.C, R49.2; also elsewhere on the board
V_MOT_IN: C39.2, U20.3 (EN), U20.6 (ANODE), U22.1 (S), U22.2 (S), U22.3 (S); also elsewhere on the board

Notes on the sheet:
Vreg 3.3V
Backfeed Protection
Boost V_Gate
~10V
4.5x3.2mm - 4.5x4mm
5V VM buck
https://datasheets.maximintegrated.com/en/ds/MAX5033.pdf MAX5033
5V fixed!
LQH43PN100M26L
Low ESR output cap. See MAX5033 Datasheet for selection info. Must have good input decoupling



Board: 2 copper layers, 60.0 x 110.0 mm, 164 parts (78 on the bottom side), 125 nets.

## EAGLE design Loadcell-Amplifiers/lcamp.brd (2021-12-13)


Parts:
C1, C4: 100n; C0603
C2, C3, C5: 1u; C0603
IN-: PTR1PAD1-13; P1-13
JP1, JP2: PINHD-1X3; 1X03
JP3, JP4: JUMPER-SMT_2_NC_TRACE_SILK; SMT-JUMPER_2_NC_TRACE_SILK
R1, R3: 4.7k; R0603
R2, R7: 10k; RJ9W
R5: 47; R0603
REF: TPB1,27; B1,27
U1: INA333MSOP8; MSOP8

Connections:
GND: C1.2, C2.2, C3.2, C4.2, C5.2, JP1.3, JP2.3, JP3.2, R3.1, U1.4 (V-)
unnamed: R5.1, R7.E
unnamed: R1.1, R2.A
unnamed: R2.E, R3.2
unnamed: JP4.2, R2.S
OUT: JP2.2, U1.6 (OUT)
REF: JP3.1, REF.TP, U1.5 (REF)
RG+: R7.S, U1.1 (RG+)
RG-: R5.2, U1.8 (RG-)
V+: C1.1, C2.1, C5.1, JP1.1, JP2.1, R1.2, U1.7 (V+)
VIN+: C3.1, JP1.2, U1.3 (VIN+)
VIN-: C4.1, IN-.TP, JP4.1, U1.2 (VIN-)

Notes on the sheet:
Offset
Gain
Loadcell
Output
Amplifier INA333
Decoupling
Could also use >1u for C5 When using a differential input it is recommended to use the same value for C3 and C4


Board: 2 copper layers, 20.0 x 26.0 mm, 17 parts (1 on the bottom side), 12 nets.

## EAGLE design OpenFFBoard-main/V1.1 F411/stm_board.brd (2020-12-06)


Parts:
C1, C2: 15pF; C0603
C3, C10: 4.7µF; C0805
C4, C5, C6, C7, C8, C9, C12: 100nF; C0603
C11: 4.7uF; C0805
D1: LV HC low drop; SMADIODE
D2: ZMM5V6; MINIMELF
H1, H2, H3, H4: MOUNT-PAD-ROUND3.0; 3,0-PAD
J1: 10118193-0001LF; FCI_10118193-0001LF
JP1: Boot; 1X02
JP2: Buttons; 2X05
JP3: Analog; 2X05
JP4: DBG/EXT; 2X08
JP5: Encoder; 1X05
JP6: SPI; 1X06
JP7: Supply; 1X02
JP8: 2516-; PAK100/2500-16
JP9: Btn; 1X02
L1: 2.2µH; L2012C
LED1: green; CHIPLED_0805
LED2: blue; CHIPLED_0805
LED3: red; CHIPLED_0805
LED4: yellow; CHIPLED_0805
R1, R5, R8: 10k; R0603
R2, R3: 22; R0603
R4: 1k; R0603
R6, R7, R9: 330; R0603
R10, R11, R12: 4.7k; R0603
SJ1: SJ
SW1, SW2: TL3342F160QG/TR
U1: STM32(LQFP64); QFP50P1200X1200X160-64N
U3: V_REG_LM1117SOT223; SOT223
X1: 8MHz; NX5032

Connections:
+3V3: C6.2, C7.1, C8.1, C9.1, C10.1, C12.1, JP1.1, JP3.1, JP3.2, JP4.8, JP4.15, JP6.5, JP8.4, JP9.1, L1.1, R4.2, R5.1, SW2.1, SW2.2, U1.1 (VBAT), U1.19 (VDD), U1.32 (VDD), U1.48 (VDD), U1.64 (VDD), U3.2 (OUT), U3.4 (OUT)
+5V: C11.1, D1.C, D2.C, JP4.16, JP5.1, JP7.2, JP8.2, R10.1, R11.1, R12.1, U3.3 (IN)
AIN0: JP3.5, U1.15 (PA1)
AIN1: JP3.6, U1.14 (PA0)
AIN2: JP3.7, U1.11 (PC3)
AIN3: JP3.8, U1.10 (PC2)
AIN4: JP3.9, U1.9 (PC1)
AIN5: JP3.10, U1.8 (PC0)
BOOT0: JP1.2, R1.1, U1.60 (BOOT0)
BRAKE_CTRL: JP8.12, U1.26 (PB0)
BUTTON_A: C6.1, JP9.2, R8.1, SW2.3, SW2.4, U1.28 (PB2)
DIN0: JP2.1, U1.4 (PC15-OSC32_OUT)
DIN1: JP2.2, U1.3 (PC14-OSC32_IN)
DIN2: JP2.3, U1.2 (PC13)
DIN3: JP2.4, U1.62 (PB9)
DIN4: JP2.5, U1.61 (PB8)
DIN5: JP2.6, U1.59 (PB7)
DIN6: JP2.7, U1.58 (PB6)
DIN7: JP2.8, U1.56 (PB4)
DRV_ENABLE: JP8.16, U1.24 (PC4)
DRV_FLAG: JP8.11, U1.25 (PC5)
ENC_A: JP5.4, R12.2, U1.37 (PC6)
ENC_B: JP5.3, R11.2, U1.38 (PC7)
ENC_Z: JP5.2, R10.2, U1.39 (PC8)
GND: C1.1, C2.1, C3.2, C4.2, C5.2, C7.2, C8.2, C9.2, C10.2, C11.2, C12.2, D2.A, H1.B3,0, H2.B3,0, H3.B3,0, H4.B3,0, J1.5 (GND), J1.S1 (SHIELD), J1.S2 (SHIELD), J1.S3 (SHIELD), J1.S4 (SHIELD), J1.S5 (SHIELD), J1.S6 (SHIELD), JP2.9, JP2.10, JP3.3, JP3.4, JP4.10, JP4.11, JP5.5, JP6.6, JP7.1, JP8.1, LED1.C, LED2.C, LED3.C, LED4.C, R1.2, R8.2, SW1.1, SW1.2, U1.12 (VSSA/VREF-), U1.18 (VSS), U1.31 (VSS), U1.47 (VSS), U1.63 (VSS), U3.1 (ADJ)
GPIO1: JP4.2, U1.52 (PC11)
GPIO2: JP4.1, U1.51 (PC10)
GPIO3: JP4.3, SJ1.1, U1.50 (PA15)
GPIO_DRV: JP8.15, SJ1.2
I2C_SCL: JP4.6, U1.41 (PA8)
I2C_SDA: JP4.4, U1.40 (PC9)
LED1: R6.2, U1.57 (PB5)
LED2: R7.2, U1.54 (PD2)
LED3: R9.2, U1.53 (PC12)
unnamed: D1.A, J1.1 (VUSB)
unnamed: LED4.A, R9.1
unnamed: C4.1, L1.2, U1.13 (VDDA/VREF+)
unnamed: C3.1, U1.30 (VCAP1/PB11)
unnamed: J1.2 (D-), R2.2
unnamed: J1.3 (D+), R3.2
unnamed: LED1.A, R4.1
unnamed: LED2.A, R6.1
unnamed: LED3.A, R7.1
NRST: C5.1, JP4.7, JP8.3, R5.2, SW1.3, SW1.4, U1.7 (NRST)
OSC+: C1.2, U1.5 (PH0-OSC_IN), X1.P$2
OSC-: C2.2, U1.6 (PH1-OSC_OUT), X1.P$1
SPI1_MISO: JP8.6, U1.22 (PA6)
SPI1_MOSI: JP8.5, U1.23 (PA7)
SPI1_SCK: JP8.8, U1.21 (PA5)
SPI1_SS1: JP8.7, U1.20 (PA4)
SPI1_SS2: JP8.9, U1.27 (PB1)
SPI1_SS3: JP8.10, U1.29 (PB10)
SPI2_MISO: JP6.2, U1.35 (PB14)
SPI2_MOSI: JP6.1, U1.36 (PB15)
SPI2_SCK: JP6.3, U1.34 (PB13)
SPI2_SS: JP6.4, U1.33 (PB12)
SWCLK: JP4.13, U1.49 (PA14)
SWDIO: JP4.9, U1.46 (PA13)
SWO: JP4.5, U1.55 (PB3)
UART1_RX: JP4.14, U1.43 (PA10)
UART1_TX: JP4.12, U1.42 (PA9)
USB_D+: R3.1, U1.45 (PA12)
USB_D-: R2.1, U1.44 (PA11)
V_EXT: JP8.13, U1.16 (PA2)
V_INT: JP8.14, U1.17 (PA3)

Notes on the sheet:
Oscillator
USB
Boot1/Function Button
Reset Button
Buttons
Jumpers
Leds
Voltage Regulator
I/O
Driver Connector
Caps
STM32
Swap LED3 to PC10


Board: 2 copper layers, 60.0 x 60.0 mm, 51 parts (1 on the bottom side), 65 nets.

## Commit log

2020-03-21 Added TMC driver
    [motor_board_tmc.brd, motor_board_tmc.sch]
2020-04-16 Changing clearances to 8 mil and renamed shunt amps
    [motor_board_tmc.brd, motor_board_tmc.sch]
2020-08-17 Updated TMC4671 board to redesigned 1.2 version.
    [BOM.ods, motor_board_tmc.brd, motor_board_tmc.sch]
2020-09-19 Added 1.1.1 stm board
    [stm_board.brd, stm_board.sch]
2020-10-22 Updated TMC Board. Fixed D12 value
    [BOM.ods, motor_board_tmc.brd, motor_board_tmc.sch]
2020-11-13 Updated STM Board to v1.2
    [JLC BOM STM FFBoard.xlsx, stm_board.brd, stm_board_f407.brd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]
2020-11-14 Fixed swapped PWM channel labels
    [stm_board_f407.brd]
2020-11-14 Added E-Stop cap
    [JLC BOM STM FFBoard.xlsx, motor_board_tmc.brd, stm_board_f407.brd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]
2020-12-06 Updated crystal capacitor value
    [JLC BOM STM FFBoard.xlsx, motor_board_tmc.sch, stm_board.brd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]
2021-01-08 Fixed swapped sense resistor labels in BOM for TMC
    [BOM.ods]
2021-01-10 Fixed tmc silkscreen (Resistor names, labels)
    [BOM.ods, motor_board_tmc.brd, stm_board_f407.brd]
2021-02-11 Added F407 board schematic pdf
    [stm_board_f407.brd]
2021-04-18 Swapped encoder Z pin on F407 board
    [stm_board_f407.brd]
2021-09-26 Schematic for f407 updated
    [stm_board_f407.sch]
2021-12-13 Added load cell amplifier files
    [JLC BOM - LCAMP.xlsx, JLCSMT - LCAMP.xlsx, lcamp.brd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]
2022-01-14 Added files for Hall sensor TMC
    [BOM.ods, motor_board_tmc.brd, motor_board_tmc.sch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]
2022-06-02 Added USB-C V1.2.3 ffboard
    [JLC BOM STM FFBoard.xlsx, stm_board_f407_1.2.3.brd, stm_board_f407_1.2.3.sch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]
2022-06-23 Fixed error in TMC V1.2 bom
    [BOM.ods]
2022-06-23 Added 32 button SPI input module design files
    [BOM - SPIBUTTONS.xlsx, SMT - SPIBUTTONS.xlsx, shiftregisterbuttons.brd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]
2022-06-23 Added SPI buttons readme
    [shiftregisterbuttons.brd]
2022-08-14 Removed C27 and C28 from BOM
    [motor_board_tmc_1.2.2.ods]
2022-08-14 Added F407 V1.2.4 files
    [BOM_FFBoard.xlsx, JLC BOM STM FFBoard.xlsx, stm_board_f407_1.2.4.brd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]
2022-08-17 Added mention of max5033busa
    [motor_board_tmc_1.2.2.ods]
2022-11-25 Updated BOM for TMC V1.2.2 hall and STM V1.2.4
    [BOM_FFBoard.xlsx, motor_board_tmc_1.2.2.ods]
2023-02-11 SPI button update
    [shiftregisterbuttons.brd]
2023-02-11 Added BISS-C adapter
    [BOM.xlsx, bisstransceiver.brd, bisstransceiver.sch]
2023-04-03 Made F407 pin1 marker more visible
    [stm_board_f407_1.2.4.brd, stm_board_f407_1.2.4.sch]
2023-07-16 Renamed CLIP LED to FFB
    [stm_board_f407_1.2.4.brd]
2023-07-26 Replaces 2.2r with 22r in v1.2.2 tmc
    [motor_board_tmc_1.2.2.ods]
2023-09-16 Added TMC 1.3.3 version
    [BOM.xlsx, motor_board_tmc.brd, motor_board_tmc.sch]
2025-03-03 Updated SPI buttons to v1.2
    [BOM - SPIBUTTONS.xlsx, SMT - SPIBUTTONS.xlsx, shiftregisterbuttons.brd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]
2025-03-03 Added lasercut case
    [Bottom_nosides.dxf, Components.xlsx, Top_nosides.dxf]

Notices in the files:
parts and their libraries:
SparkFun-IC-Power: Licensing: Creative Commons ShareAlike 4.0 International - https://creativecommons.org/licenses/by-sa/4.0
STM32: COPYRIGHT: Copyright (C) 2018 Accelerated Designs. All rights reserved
